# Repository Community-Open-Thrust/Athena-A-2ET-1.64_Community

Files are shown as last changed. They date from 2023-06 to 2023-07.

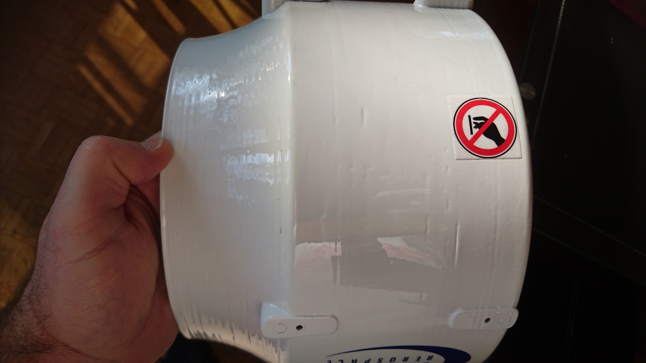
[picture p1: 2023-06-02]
Extra_Docs/Photos/Athena_DoNotTouch_Sticker_PrintedImprimé-preferably-round.JPG

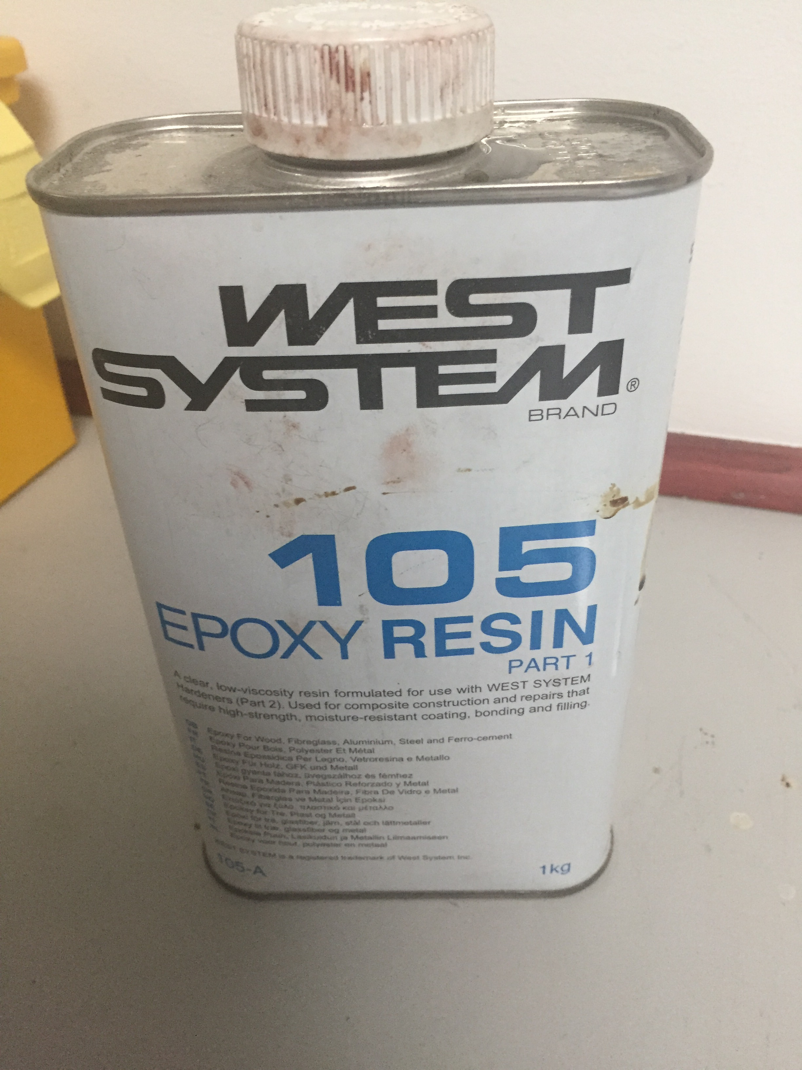
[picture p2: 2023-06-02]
Manufacturing_Info/Epoxy_Resin_105_West_System_IMG_6317.JPG

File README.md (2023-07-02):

# Athena-A-2ET Electric Ducted Fan (EDF) -  Community Edition
Athena-A 2ET - 2 stages electric ducted fan for static thrust - Community Edition - CERN-OHL-S (strongly reciprocal)

Athena_1-2ET-1 6x_Logo_BluePrint_Style

This is the repository for the Community Edition Release of the legacy to the community of makers from Neva Aerospace Ltd (UK) for the Athena Static Thrust Electric Ducted Fan (EDF) (Electric Turbine ) (Turbine électrique de poussée statique).
The Athena-A-2ET- is a 2 stages contra-rotative elecric ducted fan optimised for static thrust (hovering) in atmospheric conditions with maximum linear speed under 50kph (30mph).

The maximum thrust last checked in 2023 where between 3.7kgf to 4.1Kgf. It depends on the make of the Athena with 6S motors(2x550w) and e3D Printed parts.

# THE LICENSE IS CERN-OHL-S (Strongly Reciprocal) 
https://ohwr.org/cern_ohl_s_v2.pdf


Any further fork and/or modification must bear the following Notice as per chapter 1.10 of Definition of the OHL-s :
"acknowledgement of the Original Authors: Neva-Aero and the Human Team Members between 2013 and 2022 : F.M. Robert Vergnes, Laurent Martin, David Brotherton-Ratcliffe, Renaud-Pierre Blanpain, Daniel Schübeler, Sandro Pinent, Anthony Gambus, Tal Stokes, Valentin Bertrand, Tomas Valaitis, Louis Fourdan, Elie de Fonclare, Gilles Coïa, Domantas Brucas"

# About 3D Printing
All 3D printed parts must be in Polycarbonate in order to sustain mechanical constraints and temperature.

Only blades can be Printed in PLA with epoxy light coating.

All rotors must be balanced after assembly before mounting to the turbine.

# About using this repository
This Main repository will not change.

The Initial Commit Release date for the Main Repository is 30th of June 2023 and is for the Athena-A-2ET-1.64 (known as Athena 1.64 )

The main of repository will be locked to the initial commit to avoid losing information.

If you want to download or participate, please check the branch for the last version of the project.

If you want to participate please contact the Open-Thrust Core Team.

If you want to create a new branch for a new version please do fork or contact the Open-Thrust Core Team.

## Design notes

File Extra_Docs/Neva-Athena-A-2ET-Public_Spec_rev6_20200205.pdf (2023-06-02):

# Athena A

ELECTRIC VTOL TURB O-FAN

TURBIN E EL ECTRIQ UE D E POU SSÉE ST ATIQU E

ELEKTR O-TU RBO FA N

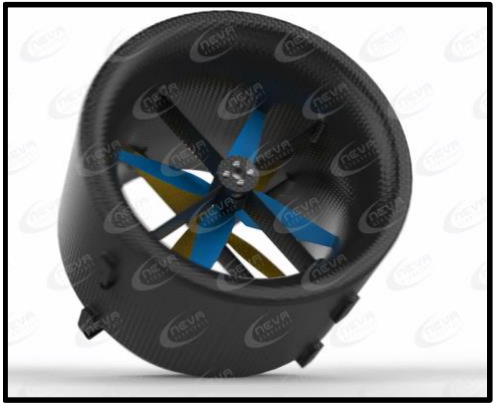
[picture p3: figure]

TECHNICAL SPECIFICATIONS – DATA SHEET | FEB. 2020

## The Neva Aerospace Athena Series are Electric Ducted Fans (EDF) engineered for efficient static flights, Vertical Take-Off

and Landing (VTOL).

## These devices are known by various names worldwide: Standschub optimimerter elektroimpeller or Elektro-turbofan in Germany, “Turbine électrique de poussée statique” in France and Electric VTOL Turbo-Fan (ETF) or static thrust Electric Ducted Fan (EDF) in the

UK and USA.

## Neva Athena Series turbines are the result of several years of R&D and provide high performance and remarkable efficiency. In particular they are designed for static thrust and are optimised for VTOL and STOL

operations.

# Key Key features:

### Safety is intrinsic in the design of all Neva EDFs, as all blades are caged: - Internal redundancy with 2 separate stages, 2 motors, and 2 ESCs (2ET-version) - Reduced size - High thrust density - Greater efficiency for static flights - high power loading as measured in

kg/kW.

### Athena A (autonomous) is offered in several variants: - 2ET: 2 stages counter-rotating (CW or CCW)*

(*) The residual torque of counter-rotating ETF can be selected as the rotation of the first stage. To be mentioned at purchase. By default we deliver 2 stages (2ET) as residual CW.

### Athena Series turbines are delivered fully assembled with Electronic Speed

Controllers (ESC), motors and propellers.

# Applications:

Typical usage for manned or unmanned aircraft: - Bespoke applications for medium sized UAS / UAV - Bespoke heavy-payload, high-safety UAV / UAA / AAM /UAM - Extreme sports (paraglider, base-jump, turbo-ski, etc…) - Security and Defence applications - Electric aviation: high -efficiency VTOL and slow speed linear flight - Airships: high efficiency thrust for VTOL & slow speed linear flight

### Athena-A-V1.x-2ET (2 stages counter-rotating)

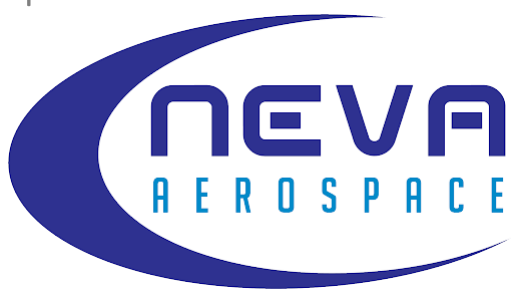
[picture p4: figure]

Copyright © 2015, 2016, 2017, 2018

Neva Aerospace Ltd.
Doc. Rev. 5.20

2/6

Made in Europe

# Contact: sales@neva-aero.com

Neva-Athena-A-2ET-Public_Spec_rev6_20200205.docx

Measurements on Athena-A-2ET-V1.6x Feb. 2018.

### Notes:

The residual torque of counter-rotating ETF can be selected as the rotation of the first stage. To be mentioned at purchase. By default we deliver 2 stages (2ET) as first stage CW with residual CW torque.
1.5x and 1.6x are in different composite materials and so have different density and weight ratio.
1.5x shroud: carbon composite, and other components: plastic composite.
1.6x all parts are plastic composite.
V1.5x and V1.6x include the ESC weight (ESC integrated within the turbine)

### Temperatures :

Operating temperatures: non-icing conditions only & avoid direct sunlight when not flying from -10 Degree Celsius to +50 Degree Celsius for Carbon shroud (1.5x)
from 0 Degree Celsius to +40 Degree Celsius for Plastic Composite shroud(1.6x)
Storage Temp: from 5 DegC to +35 DegC – no direct sunlight- dry storage50
Max Diameter of Turbine at Inlet | 250 mm
Rotor Assembly Diameter | 195 mm
Length of Shroud | 170 mmm
Weight of Turbine | 1.1 kg
Max Thrust | 4.0 kgf
Electrical Power at Max Thrust | 1.2 kW
Normal Operating Thrust | 2.9 Kgf
Power at Normal Operating Thrust | 0.8 kW
Supply Voltage | 22.4 V (6S)
Max Current | 55 A
| 0.92 Kgf @ 6.07 gf/We
Efficiency (Gross Power Loading) | 1.38 Kgf @ 5.18 gf/We
at various Thrust settings | 2.04 Kgf @ 4.32 gf/We
| 2.76 Kgf @ 3.85 gf/We
| 3.39 Kgf @ 3.33 gf/We
Material | Composite
Noise Level (@3m ) Outdoor | 84db at full power
Noise Level (@3m ) Indoor | 92dB at full power

### ATHENA-A-2ET-V1.64 (2 stages Contra-rotating)

3/6

# Contact: sales@neva-aero.com

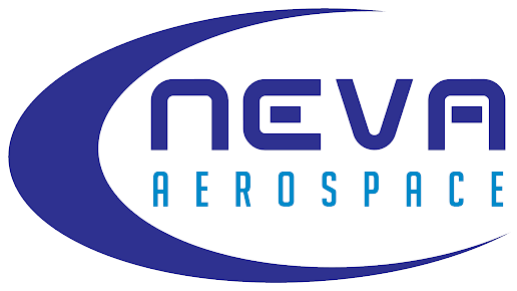
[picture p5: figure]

Neva-Athena-A-2ET-Public_Spec_rev6_20200205.docx

## ATHENA-A ELECTRIC VTOL TURBO-FAN Made in Europe

## Notes on Technical Specifications:

Units used:
International System of Units (SI Metric): kg= kilogram, g=gram, kgf=kilogram force means thrust measured in kilograms; g/We (or gf/W) means efficiency in gram-force-thrust per Watt electric consumed.
Weight & Control Systems:
ESC means Electronic Speed Controller
The weight of our turbofans includes shroud, motors, propellers, and motor holder(s) but not the ESCs.
ESCs are delivered together with the EDF.
Motors:
Depending on your applications we mount 2 types of electric motor with different power, please contact us for motor specifications.
Accuracies:
All figures are given with a +/- 5% accuracy.
All thrusts in gf or in kgf and efficiencies (power loadings) in gf/We or kgf/We represent gross values and are given with reference to the International Standard Atmosphere for dry air (ICAO 1964) and as such pertain to measurements at 15 degrees Celsius at 1013.25hPa and zero humidity.
Updates:
Specifications are subject to be updated without notice.
Please contact us to obtain the latest specifications.
Warranty Warning:
Any modification made to the ESC, motor, propellers, fan or shroud geometry, or over-clocking will void the warranty.
Icing condition: De-icing may not be fitted, and our electric turbofans are currently not acceptable for icing conditions.
Flight Level: Operational flight level up to 3281 ft (Feet) / 1000 M (Meter) Restrictions: Neva authorize and warrant the use of its electric ducted fans only for civilian applications up to 25kg MTOW aircraft (LT25) and lower than 3 000 ft. Shroud Warranty – outside of wearable parts:
Carbon shroud 3 years or 5 000 hrs
Plastic composite shroud 1 years or 2 000 hrs
Turbine Ingress Protection Code (IP): IP 53 . Please note that high level of dust or sand in atmosphere may wear blades or motor bearings more rapidly than usual.

IP
About Certifications & Flight Rules:
We make no warranties on the acceptability by the local regulator nor certification under local UAV/UAS regulation or Manned aircraft regulations. It is the full responsibility of the UAS/UAV integrator, aircraft manufacturer, to liaise with its certification body if/when need be.
Unmanned:
Our turbofans may be used for VLOS & BVLOS up to 25Kg MTOW depending on your region and local laws; and may not be suitable for BLOS according to your local rules. Applications with a MTOW higher than 25kg and/or above 3 000ft are at your own risks. To obtain warranty above MTOW 25Kg and/or 3 000 ft, you need to contact us.
Manned:
Our turbofans have to be certified within your aircraft under ULM or Prototype certification rules with your aircraft and may be suitable for VFR certification. If you embed our electric turbofan in a manned aircraft, you need to contact us to have an extension of warranty.
All information in this specification sheet is proprietary.
All images are non-contractual.

Patents (EU, USA, and INTL) granted and/or pending:
EU DM/089417, 2016-5567, US Application No. 35/5000,663 Copyright © 2015, 2016, 2017, 2018, 2019 – Neva Aerospace Ltd.

## Contact:

## Sales@Neva-Aero.com

Neva Aerospace Ltd.

### Sussex Innovation Centre Brighton BN1 9SB United Kingdom

# External Dimensions: Athena -A-2ET-V1.6x

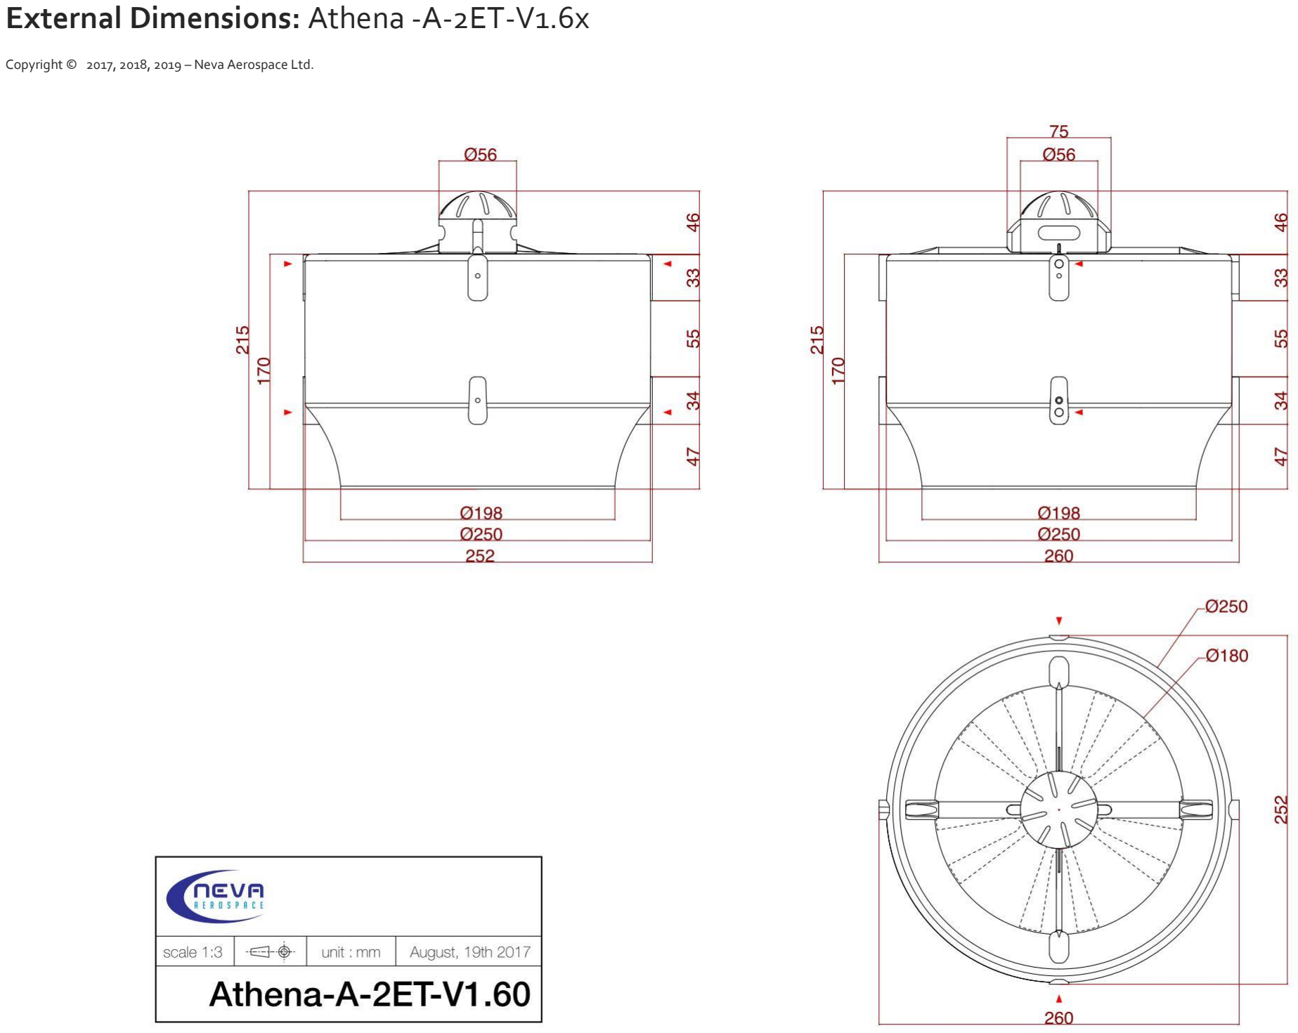
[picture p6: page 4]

Copyright © 2017, 2018, 2019 – Neva Aerospace Ltd.

## Technical Annex – Athena-A-2ET-V1.6x

## Efficiency Thrust vs Power – Athena-A-2ET-1.64 (6S)

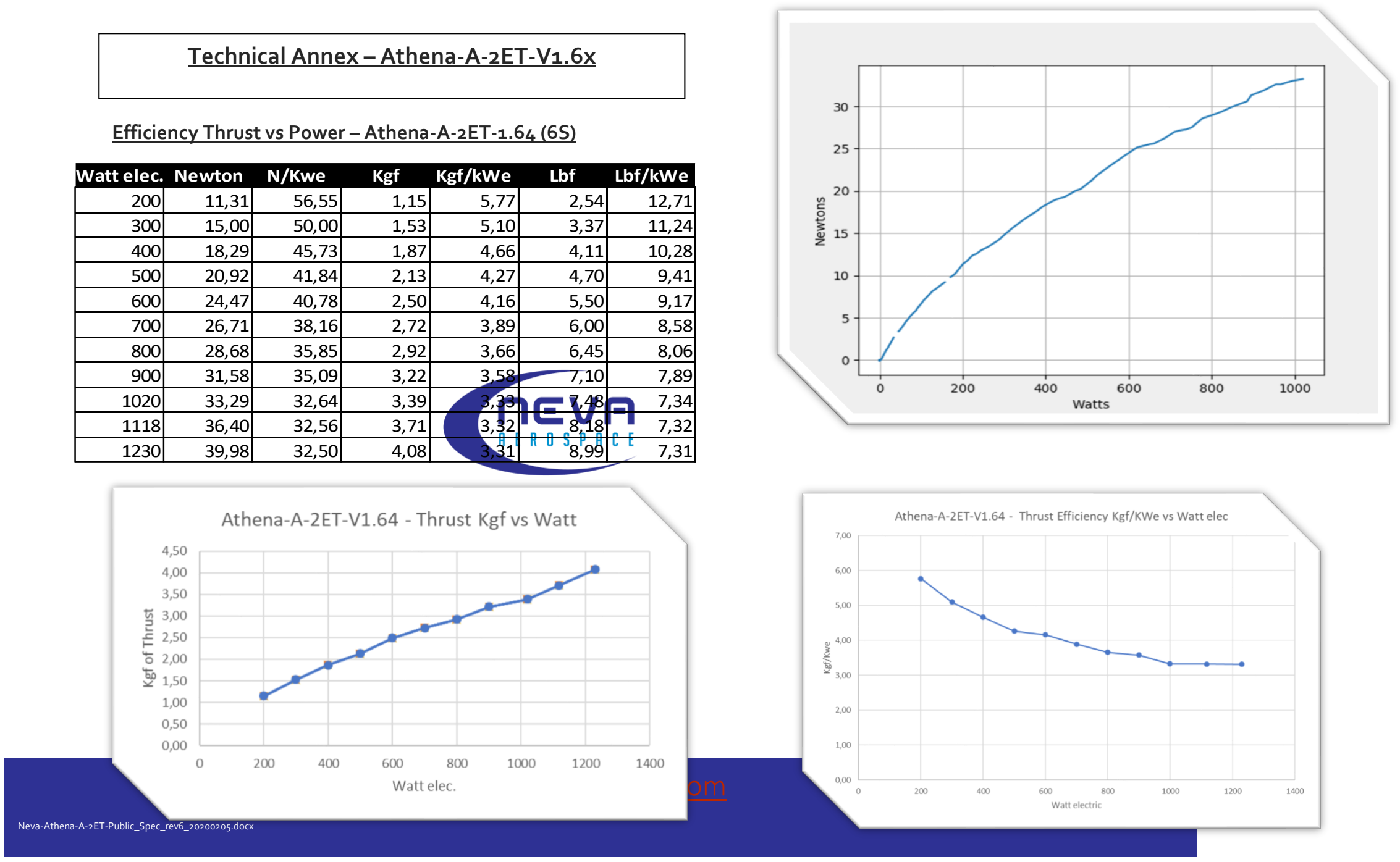
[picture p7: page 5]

5/6

# Contact: sales@neva-aero.com

Neva-Athena-A-2ET-Public_Spec_rev6_20200205.docx

Watt elec. Newton | N/Kwe | Kgf | Kgf/kWe | Lbf | Lbf/kWe
200 | 11,31 | 56,55 | 1,15 | 5,77 | 2,54 | 12,71
300 | 15,00 | 50,00 | 1,53 | 5,10 | 3,37 | 11,24
400 | 18,29 | 45,73 | 1,87 | 4,66 | 4,11 | 10,28
500 | 20,92 | 41,84 | 2,13 | 4,27 | 4,70 | 9,41
600 | 24,47 | 40,78 | 2,50 | 4,16 | 5,50 | 9,17
700 | 26,71 | 38,16 | 2,72 | 3,89 | 6,00 | 8,58
800 | 28,68 | 35,85 | 2,92 | 3,66 | 6,45 | 8,06
900 | 31,58 | 35,09 | 3,22 | 3,58 | 7,10 | 7,89
1020 | 33,29 | 32,64 | 3,39 | 3,33 | 7,48 | 7,34
1118 | 36,40 | 32,56 | 3,71 | 3,32 | 8,18 | 7,32
1230 | 39,98 | 32,50 | 4,08 | 3,31 | 8,99 | 7,31

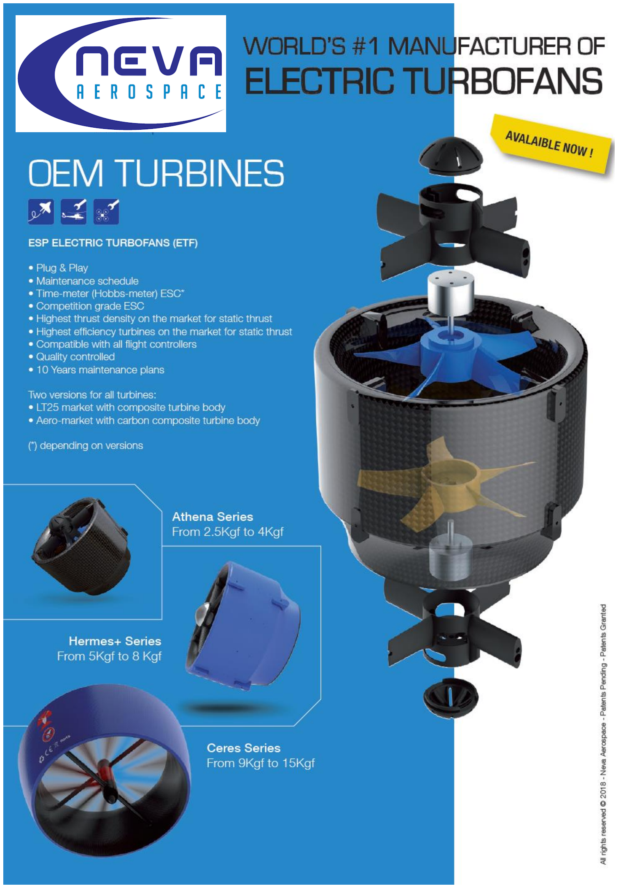
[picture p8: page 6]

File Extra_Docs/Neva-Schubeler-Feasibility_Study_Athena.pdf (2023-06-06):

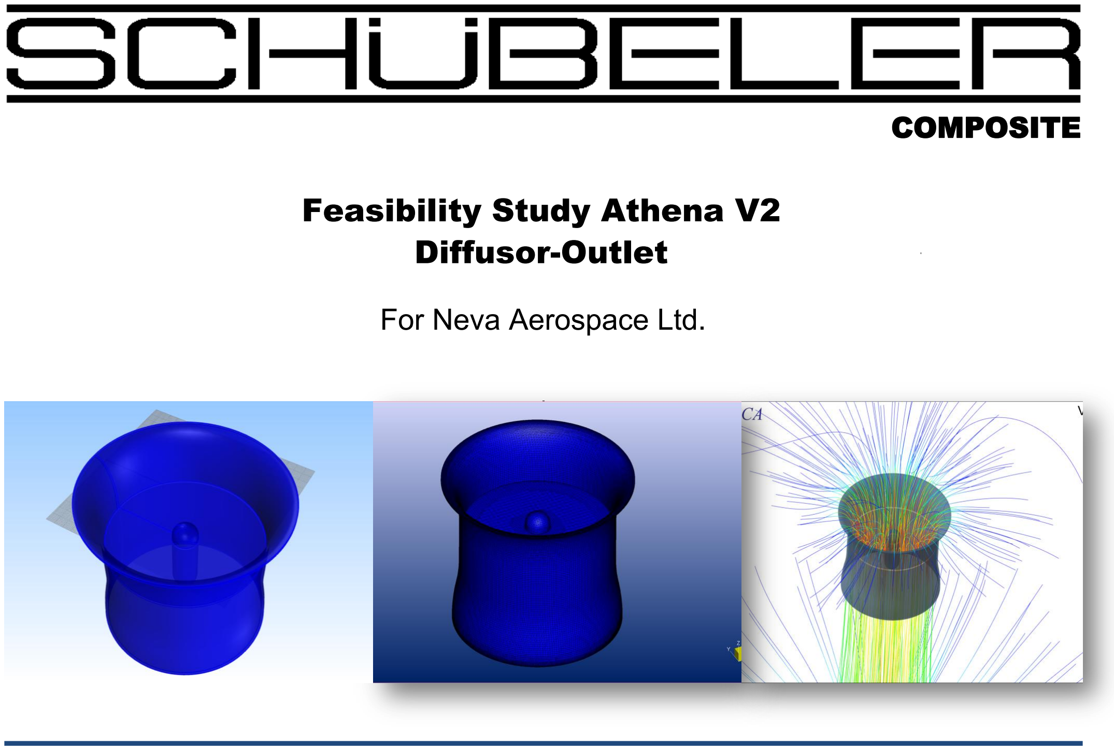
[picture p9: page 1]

COMPOSITE

Feasibility Study Athena V2

Diffusor⁻Outlet
For Neva Aerospace Ltd.

22.10.2015

Slide 2

Fa. Schübeler-Composite
Daniel Schübeler

Feasibility Study AthenaV2 Diffusor Outlet Dipl. Wirt.-Ing. Sandro Pinent

## Content

## 1. Specifications

## 2. Analytical Approach

## 3. CFD-Simulations

## 4. Conclusions

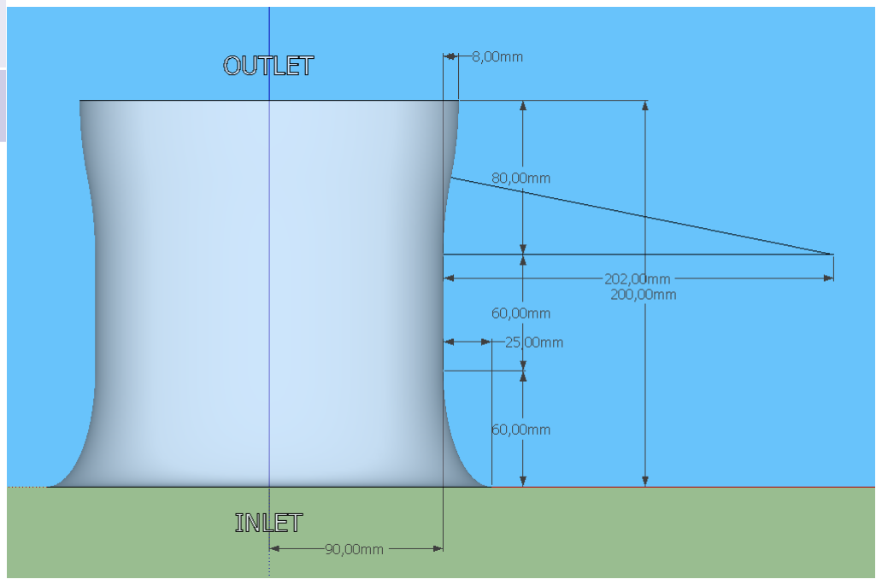
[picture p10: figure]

Slide 3

Fa. Schübeler-Composite
Daniel Schübeler

## 1. Specifications

| Athena V2
Density [kg/m³] | 1,25
Shroud Diameter [mm] | 180
Hub Diameter [mm] | 30
v0 [m/s] | 0
Thrust [N] | ~40 N

Slide 4

Fa. Schübeler-Composite
Daniel Schübeler

## 2. Analytical Approach

Where is the Lift generated?

- Momentum change

OR

- Thrust due to pressure distribution and viscous stress on solids

### v mv

dt

### dm T I

### I mv

- =
= =

=

ò | ò
= | · · | +
solid | Asolid
viscous | solid
A
T | p n dAsolid | τ | dA

## 2. Analytical Approach

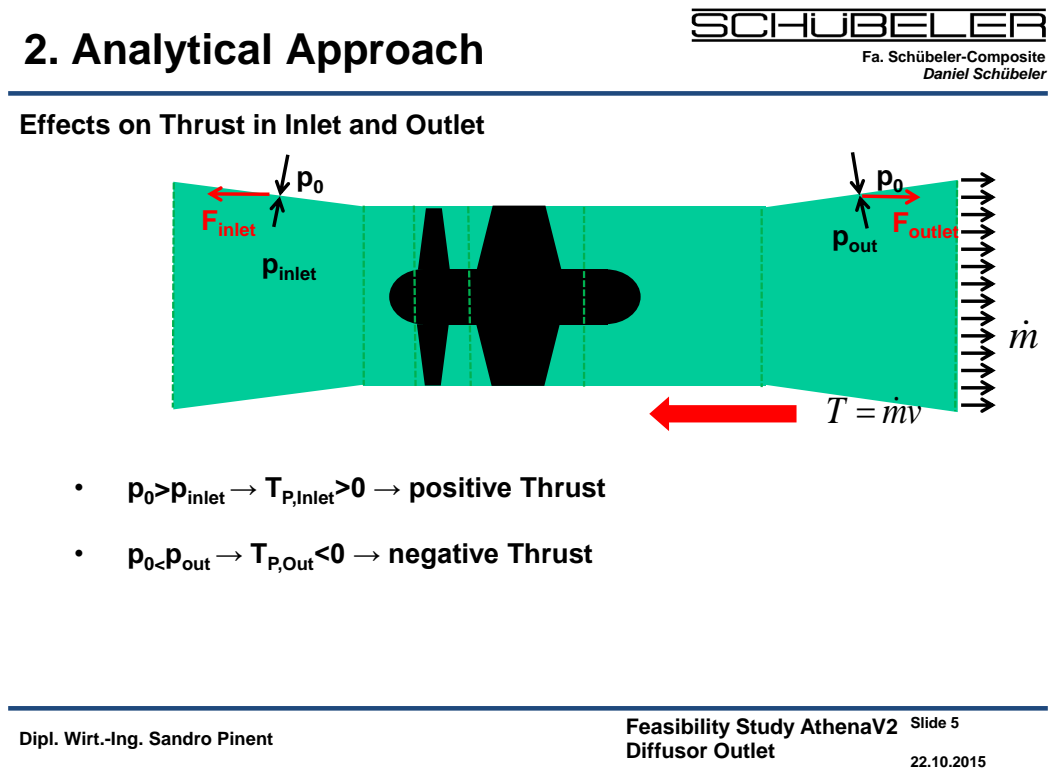
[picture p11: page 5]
Slide 5; Daniel Schübeler; pinlet; Finlet; pout; Foutlet

Fa. Schübeler-Composite

Effects on Thrust in Inlet and Outlet

• p0>pinlet→ TP,Inlet>0 → positive Thrust

• p0<pout → TP,Out<0 → negative Thrust

## 2. Analytical Approach

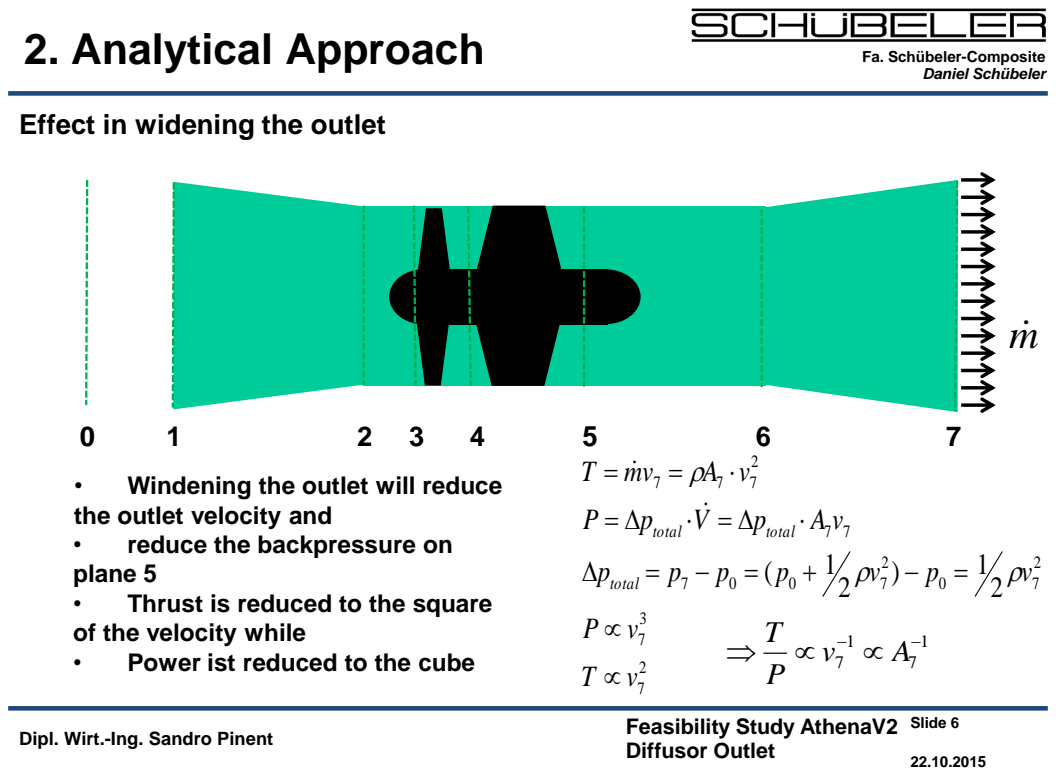
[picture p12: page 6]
Slide 6; Daniel Schübeler; total

Fa. Schübeler-Composite

Effect in widening the outlet

• Windening the outlet will reduce
the outlet velocity and
• reduce the backpressure on
plane 5
• Thrust is reduced to the square
of the velocity while
• Power ist reduced to the cube

## 2. Analytical Approach

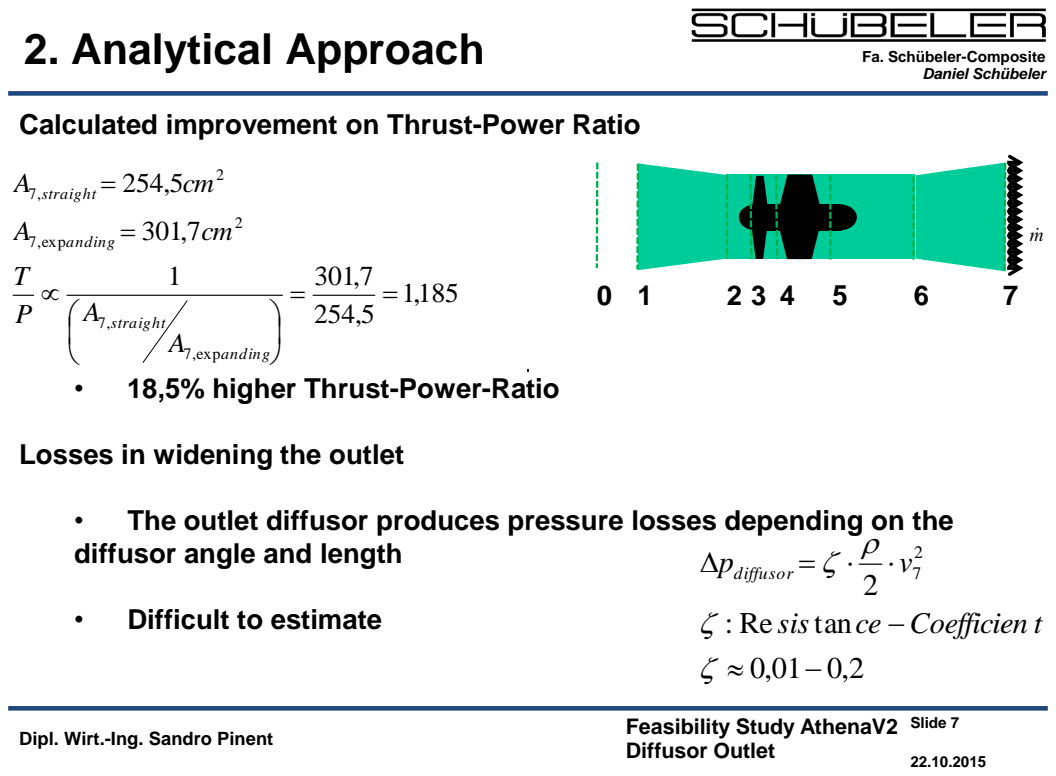
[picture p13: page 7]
Slide 7; Daniel Schübeler; tan; sis; ce Coefficien t; v diffusor; 7,exp; anding; straight

Fa. Schübeler-Composite

Calculated improvement on Thrust-Power Ratio

• 18,5% higher Thrust-Power-Ratio

Losses in widening the outlet

• The outlet diffusor produces pressure losses depending on the
diffusor angle and length

• Difficult to estimate

Slide 8

Fa. Schübeler-Composite
Daniel Schübeler

## 2. Analytical Approach

Unlimited Thrust?

- In Theory, yes
- Until the diffusor losses are bigger than the Thrust increase
- Reducing the outlet velocity means loss of agility
- What are the limits for the diffusor?

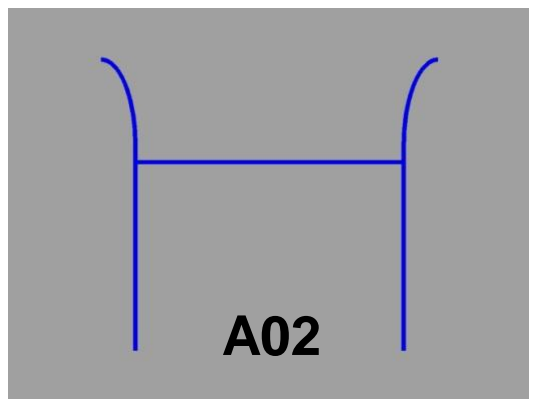
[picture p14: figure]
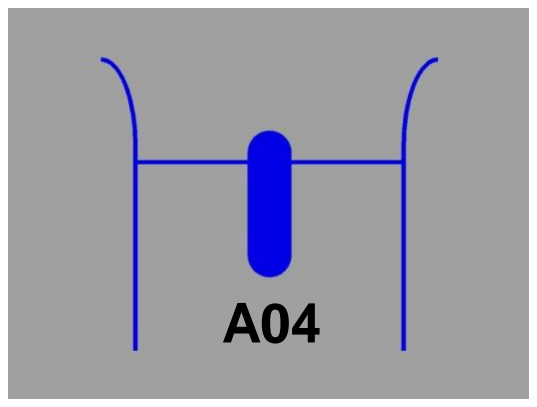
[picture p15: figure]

Slide 9

Fa. Schübeler-Composite
Daniel Schübeler

## 3. CFD-Simulations

Geometry:
- 4 Geometries calculated
- With hub and without hub
- With expanding nozzle and without

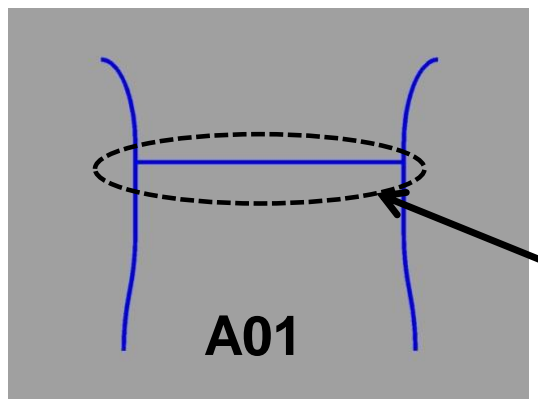
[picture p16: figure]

A03 | A04

Actuator Disc:
-Outlet at upper side
-Inlet at lower side
-same massflow

## 3. CFD-Simulations

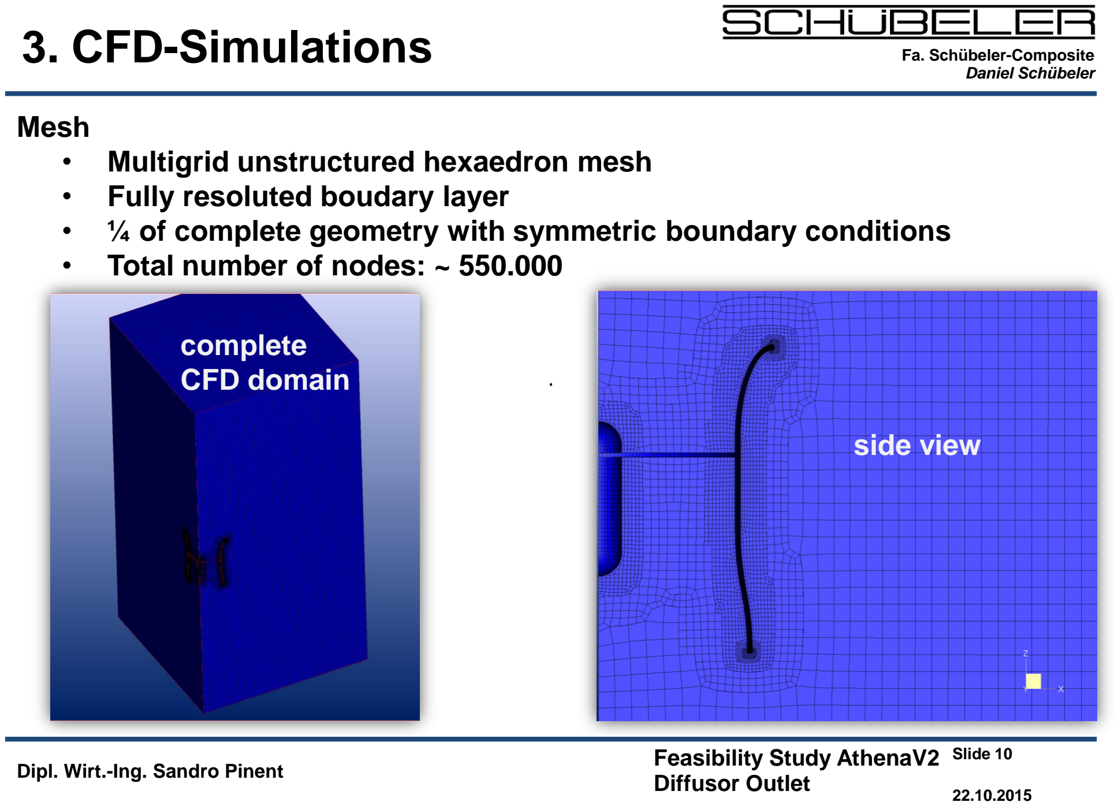
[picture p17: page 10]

Slide 10

Fa. Schübeler-Composite
Daniel Schübeler

Mesh
- Multigrid unstructured hexaedron mesh
- Fully resoluted boudary layer
- ¼ of complete geometry with symmetric boundary conditions
- Total number of nodes: ~ 550.000

complete
CFD domain

side view

## 3. CFD-Simulations

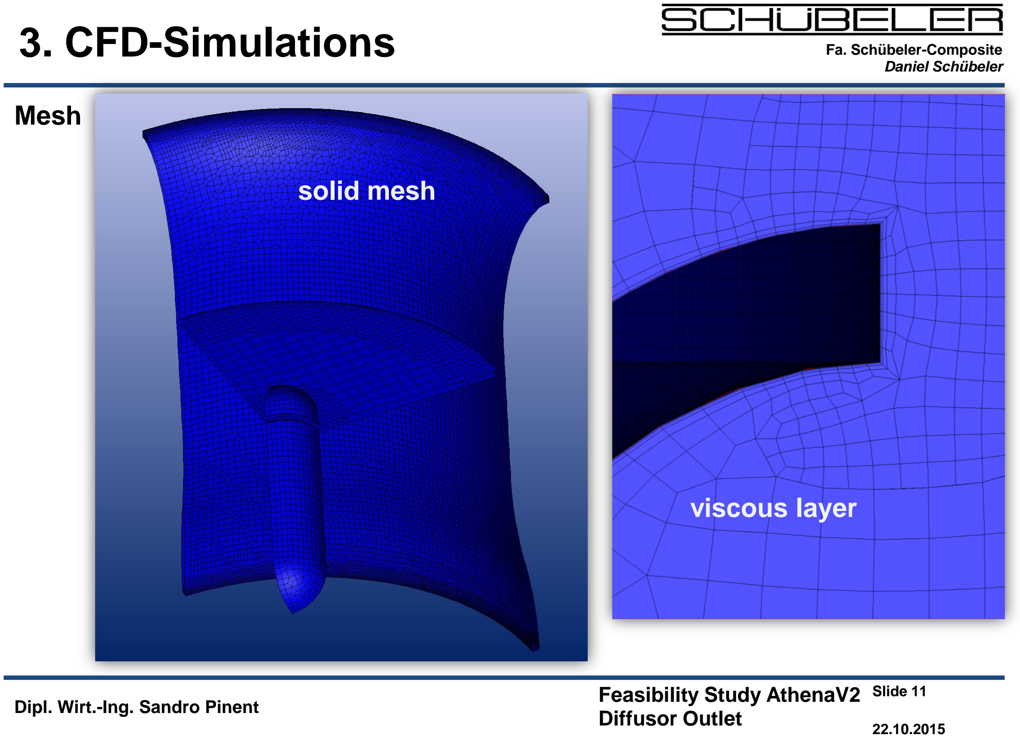
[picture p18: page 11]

Slide 11

Fa. Schübeler-Composite
Daniel Schübeler

Mesh

solid mesh

viscous layer

Slide 12

Fa. Schübeler-Composite
Daniel Schübeler

## 3. CFD-Simulations

Solver Setting

- Compressible fluid model „Air Perfect“
- Mathemetical model: Navier Stokes
- Spalart Almaras turbulence model
- CFL number: 3
- Steady state

Slide 13

Fa. Schübeler-Composite
Daniel Schübeler

## 3. CFD-Simulations

Boundary Conditions

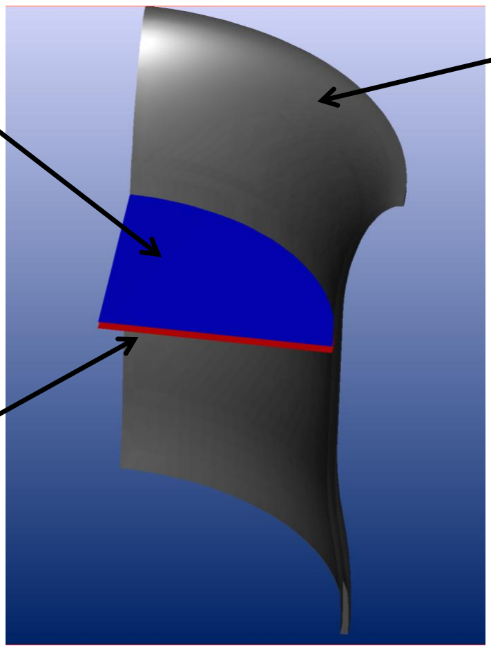
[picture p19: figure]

Outlet:
1,049 kg/s

Inlet:
1,049 kg/s

Solids:
smooth Wall

Externals:
v=0 m/s
p=102325
T=288,15 K

## 3. CFD-Simulations

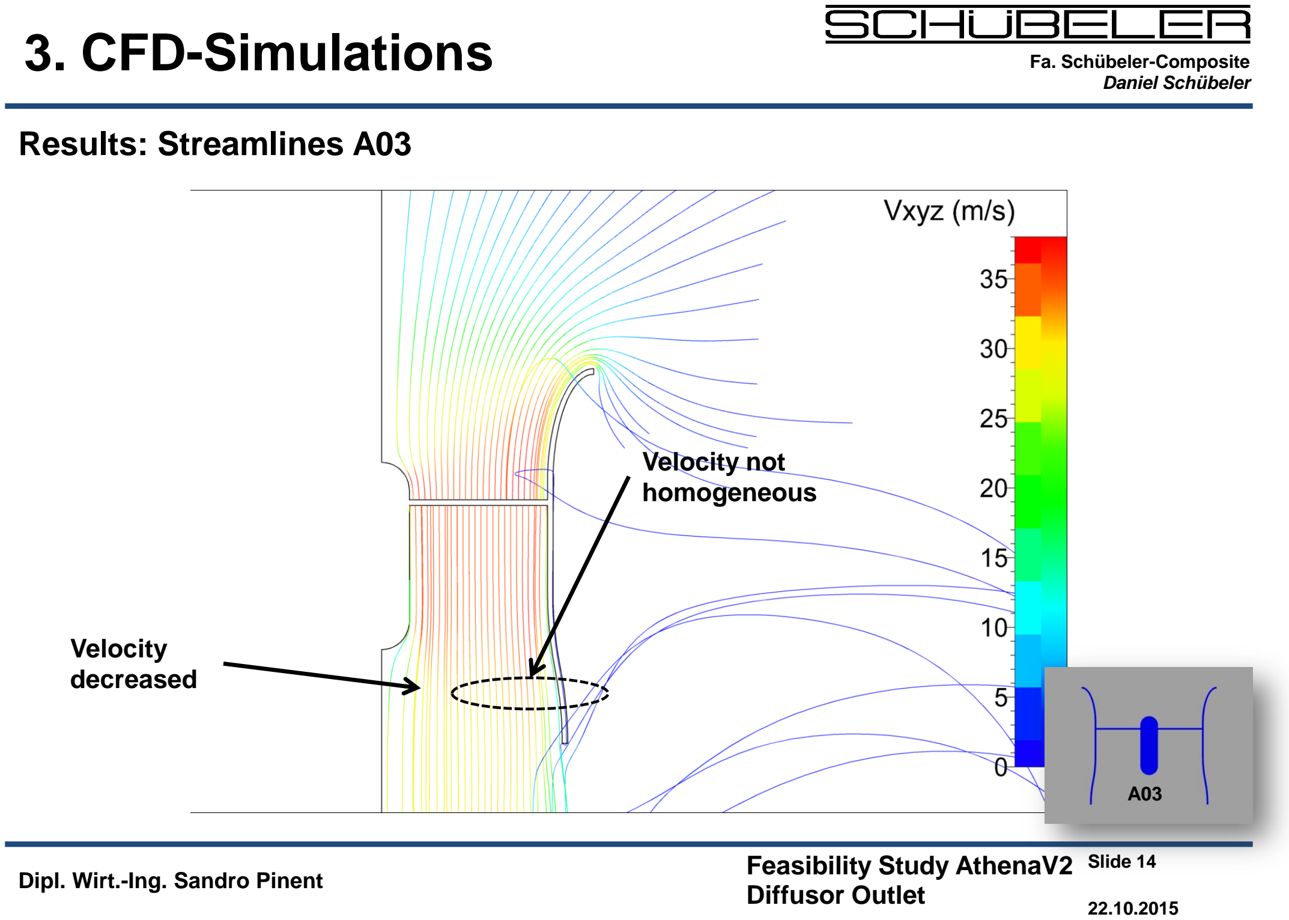
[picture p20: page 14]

Slide 14

Fa. Schübeler-Composite
Daniel Schübeler

Results: Streamlines A03

Velocity
decreased

Velocity not
homogeneous

A03

## 3. CFD-Simulations

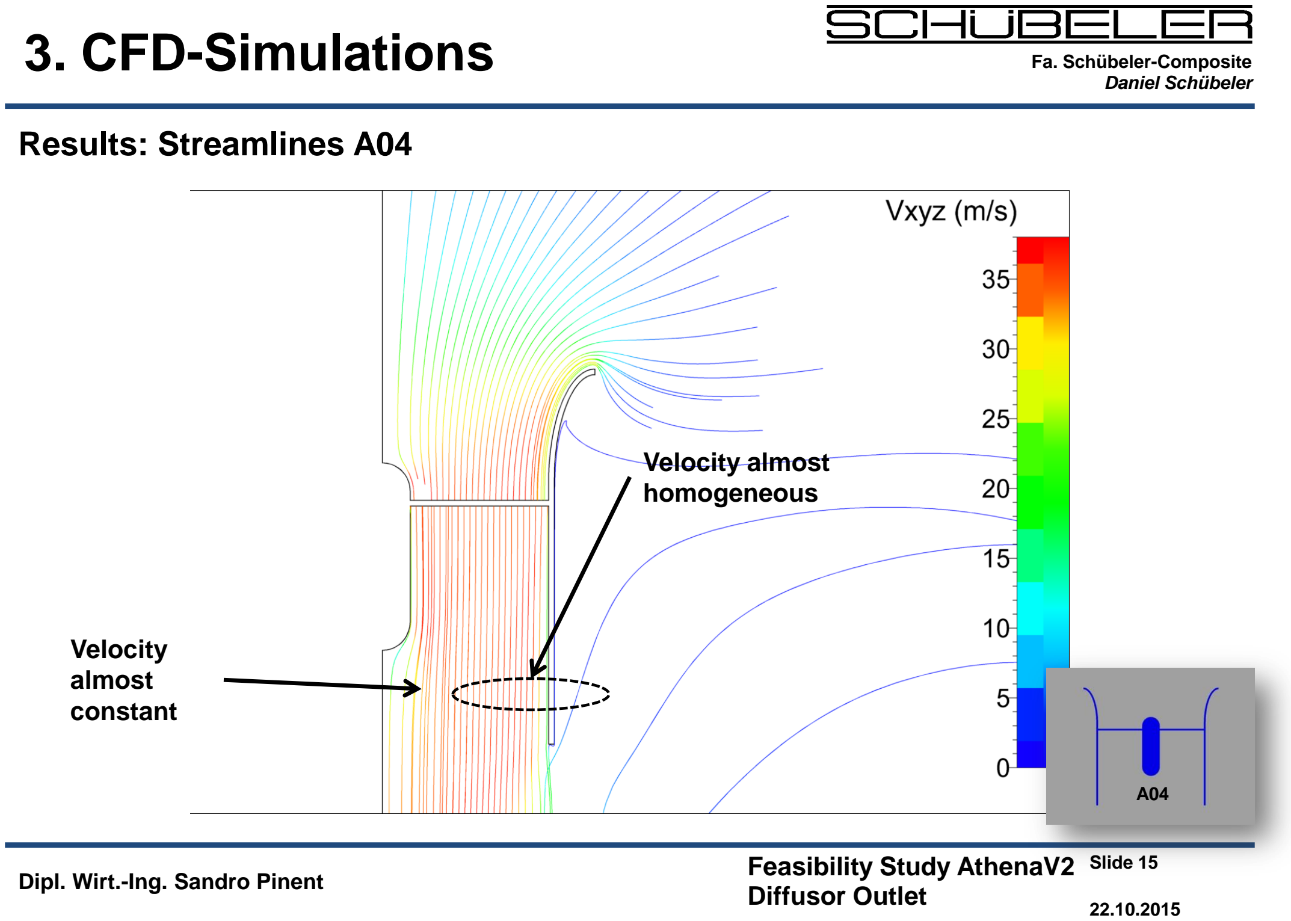
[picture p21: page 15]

Slide 15

Fa. Schübeler-Composite
Daniel Schübeler

Results: Streamlines A04

Velocity
almost
constant

Velocity almost
homogeneous

A04

## 3. CFD-Simulations

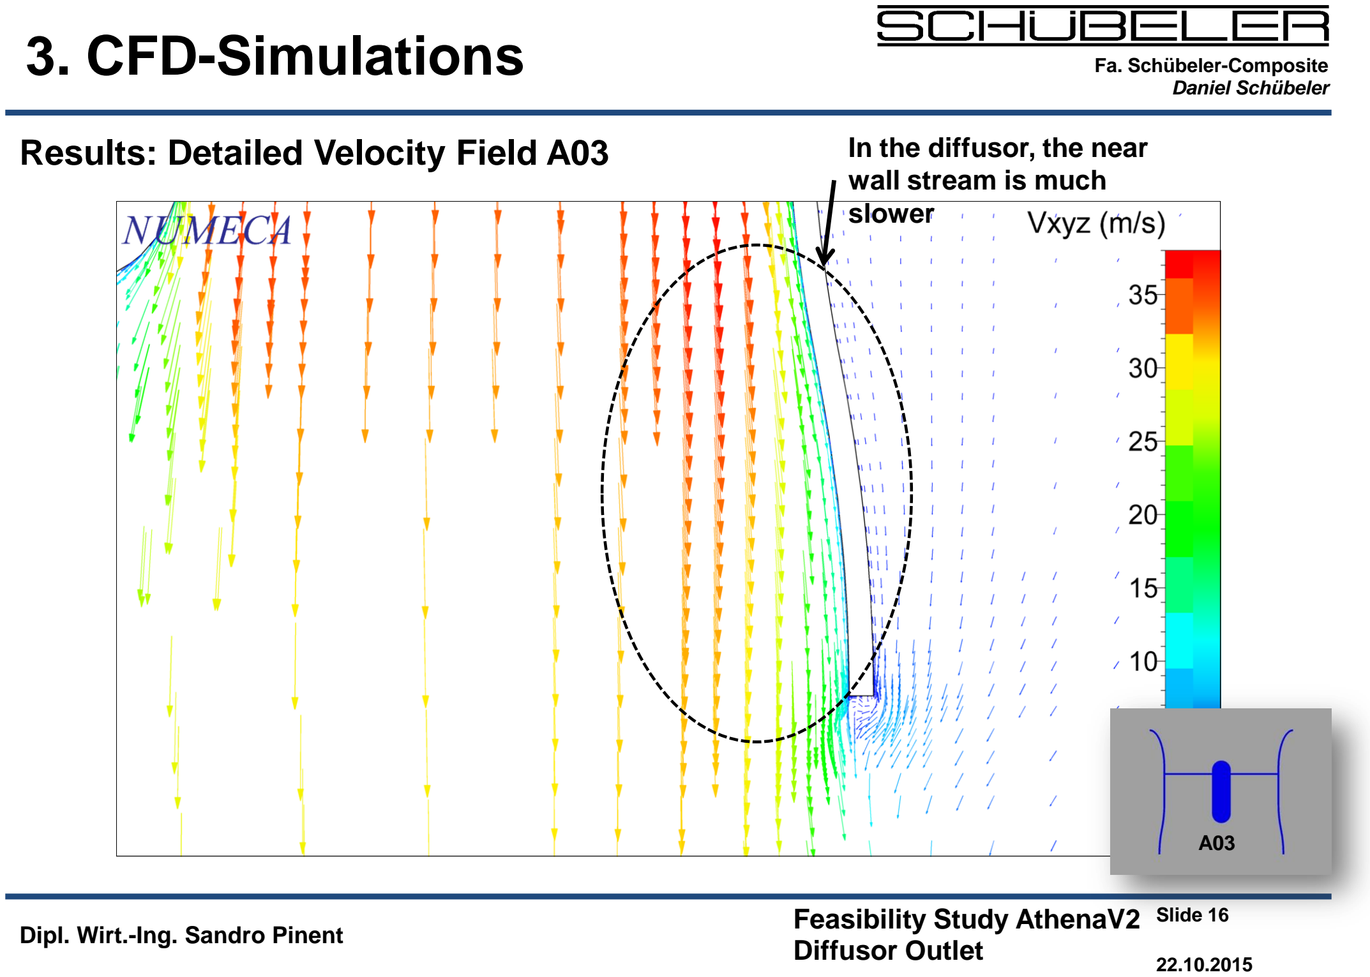
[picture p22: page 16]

Slide 16

Fa. Schübeler-Composite
Daniel Schübeler
Results: Detailed Velocity Field A03 | In the diffusor, the near wall stream is much slower

A03

## 3. CFD-Simulations

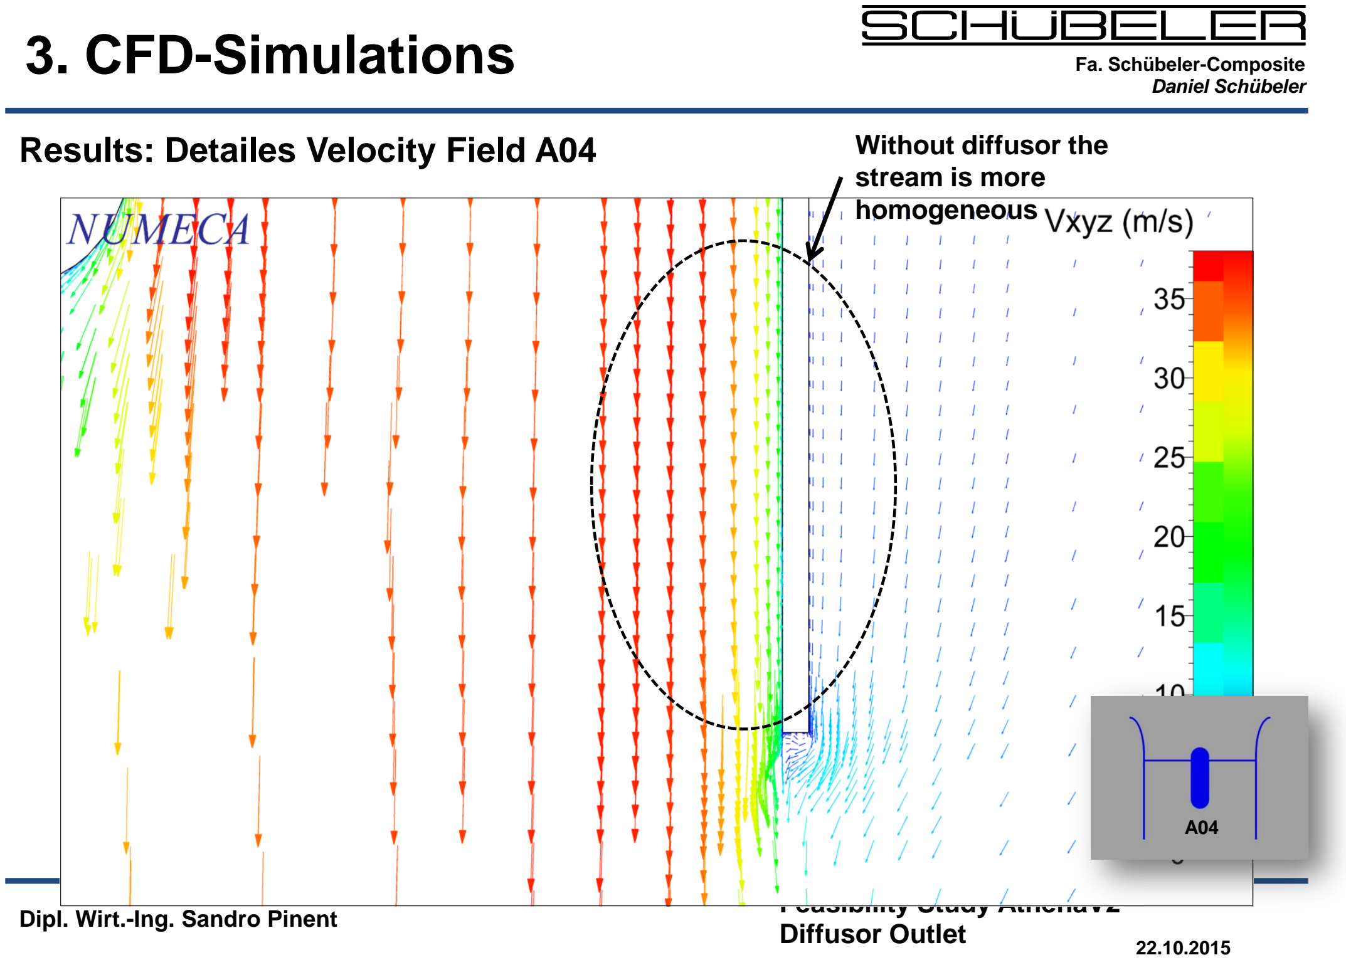
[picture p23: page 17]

Slide 17

Fa. Schübeler-Composite
Daniel Schübeler
Results: Detailes Velocity Field A04 | Without diffusor the stream is more homogeneous

A04

## 3. CFD-Simulations

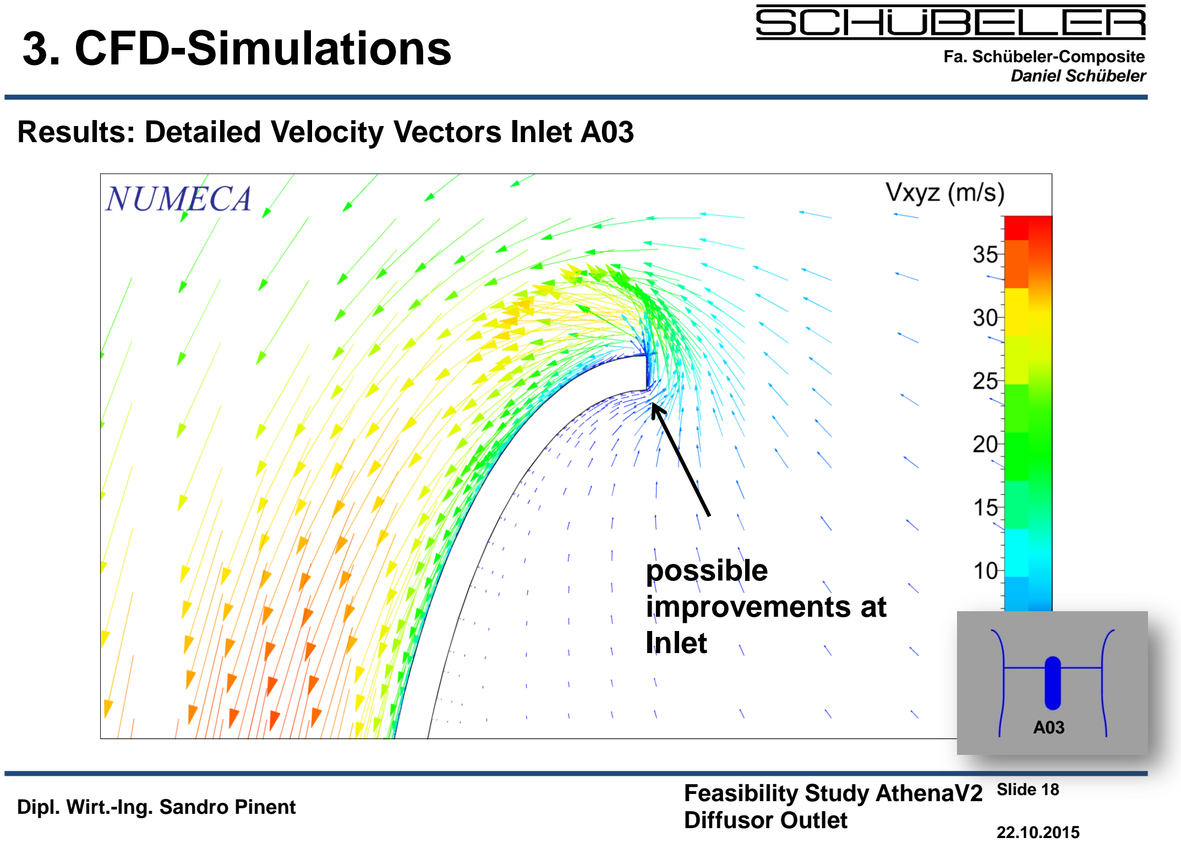
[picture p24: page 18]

Slide 18

Fa. Schübeler-Composite
Daniel Schübeler

Results: Detailed Velocity Vectors Inlet A03

A03

possible
improvements at
Inlet

## 3. CFD-Simulations

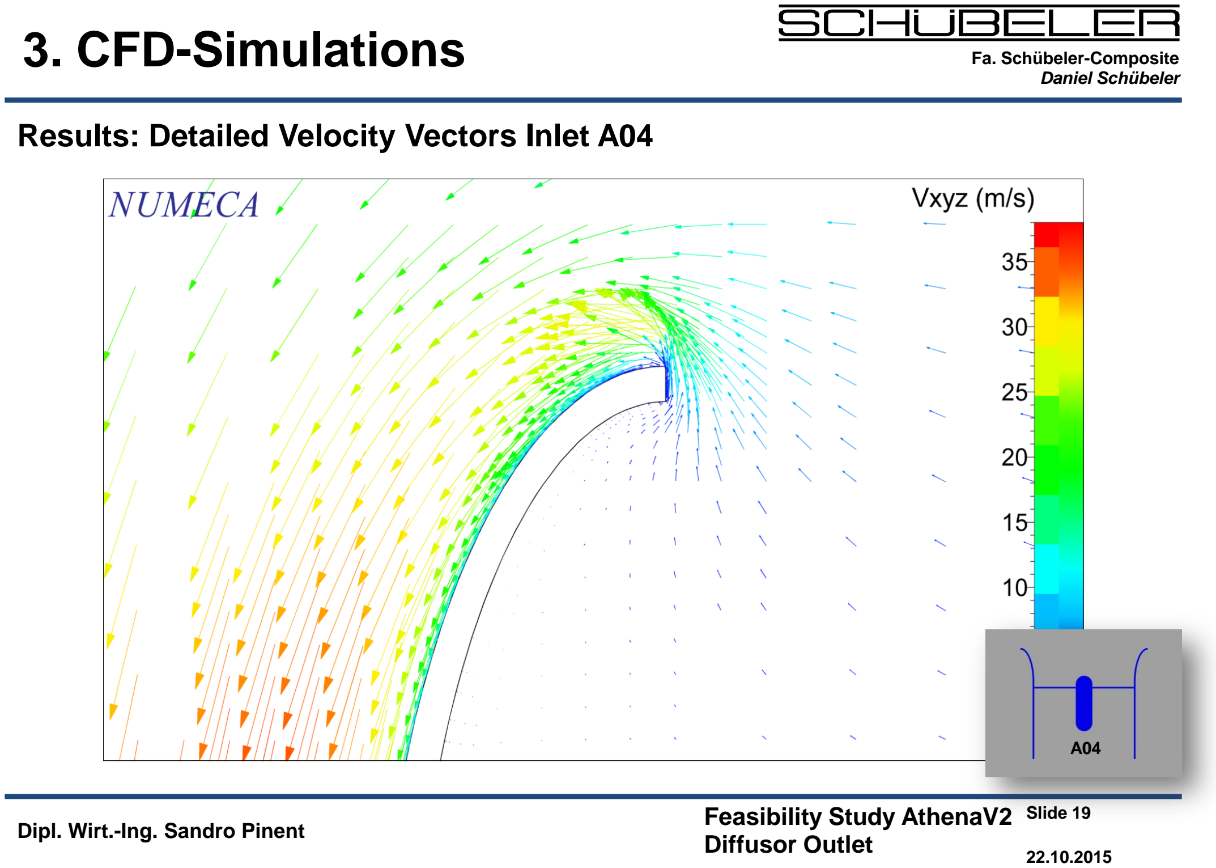
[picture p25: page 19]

Slide 19

Fa. Schübeler-Composite
Daniel Schübeler

Results: Detailed Velocity Vectors Inlet A04

A04

## 3. CFD-Simulations

Slide 20

Fa. Schübeler-Composite
Daniel Schübeler

Results: Total and Static Pressure A03

A03

## 3. CFD-Simulations

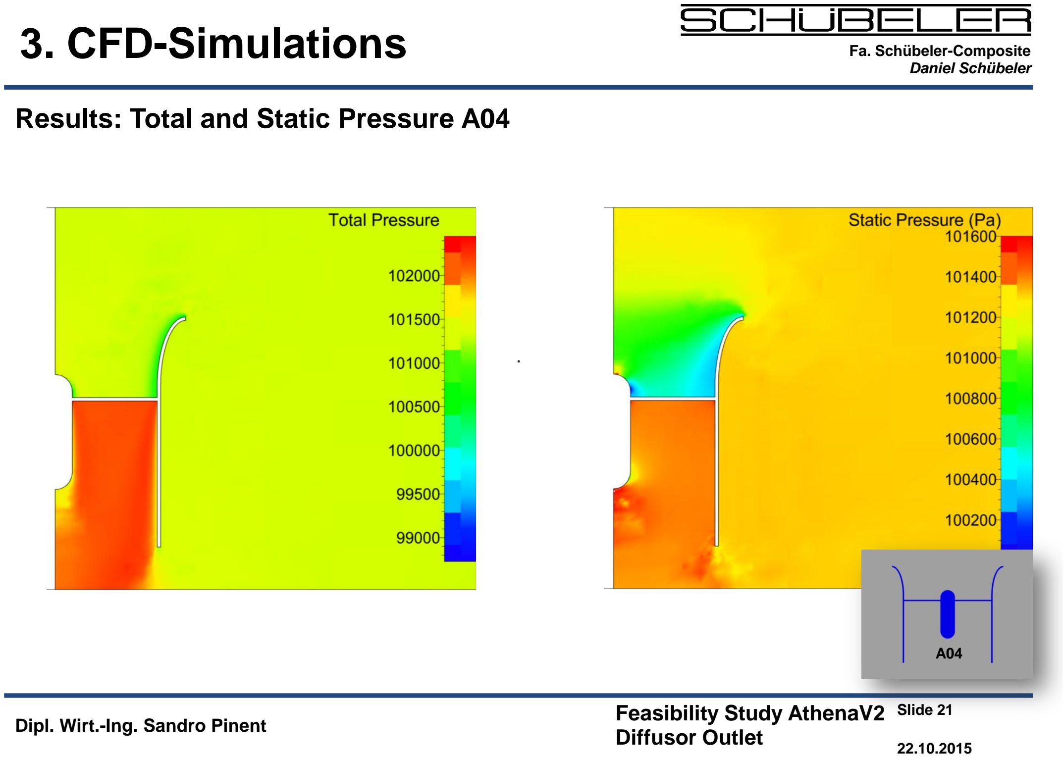
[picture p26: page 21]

Slide 21

Fa. Schübeler-Composite
Daniel Schübeler

Results: Total and Static Pressure A04

A04

Fa. Schübeler-Composite
Daniel Schübeler

## 3. CFD-Simulations

Results: Visualization of the Pressure Forces in Z-Direction A03

Slide 22

Fa. Schübeler-Composite
Daniel Schübeler

## 3. CFD-Simulations

Results: Visualization of the Pressure Forces in Z-Direction A04

Slide 23

Slide 24

Fa. Schübeler-Composite
Daniel Schübeler

## 3. CFD-Simulations

Results: Comparsion

- The diffusor outlet has 23% better Thrust-Power-ratio
- Analytically only 18% ... ?
- Only the hydraulical Power is considerated, no fan, nor motor efficiency
- To achieve this improvement, the aerodynamic rotor has to be optimized for each case. (Optimum rotor for A03 is other than A04)
- The improvement works only for static thrust
| T[N] Momentum change (mf*v) | vf[m³/s] | ptot,3 [Pa] | ptot,5 [Pa] | Δp [Pa] | Phydr [W] | T/Phydr [N/kW]
A03 | 30,45 | 0,856 | 101220 | 101867 | 647 | 553,8 | 54,9
A04 | 35,88 | 0,855 | 101220 | 102160 | 940 | 803,9 | 44,6

Fa. Schübeler-Composite
Daniel Schübeler

## 4. Conclusions

Outlook

- It may be interesting to push the diffusor to the limits
- Find the optimum diffusor in trems of diameter, length and shape
- Investigate how the diffusor behaves at other power setting

Slide 25

- Perform a complete CFD-Calculation including the complete rotating fan

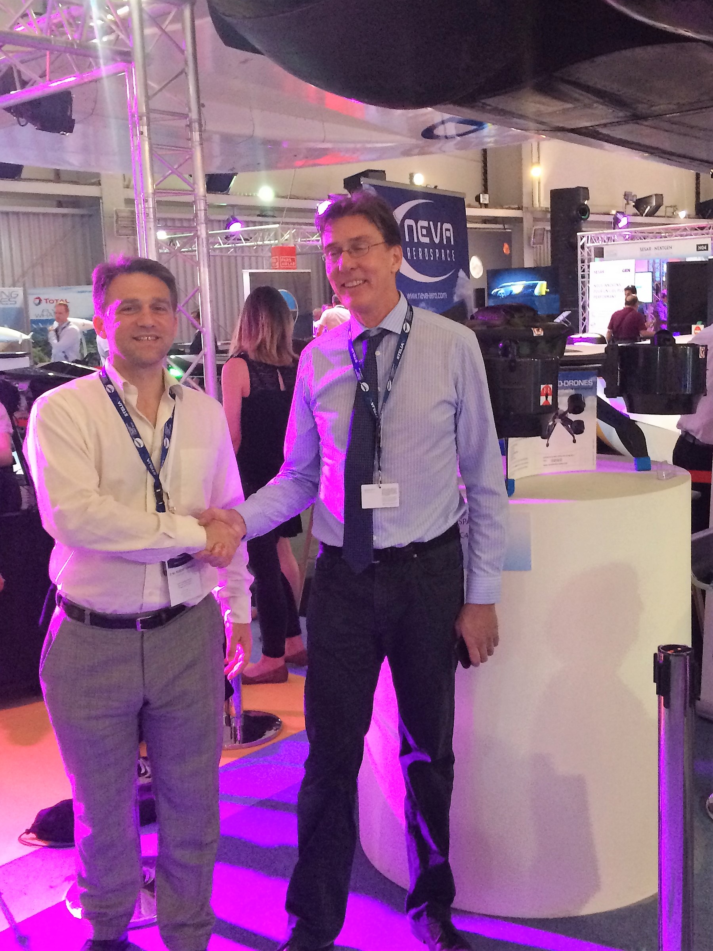
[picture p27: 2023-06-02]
Extra_Docs/Photos/Exhibitons_various/R_Vergnes_D_Ratcliffe_IMG_0991.JPG

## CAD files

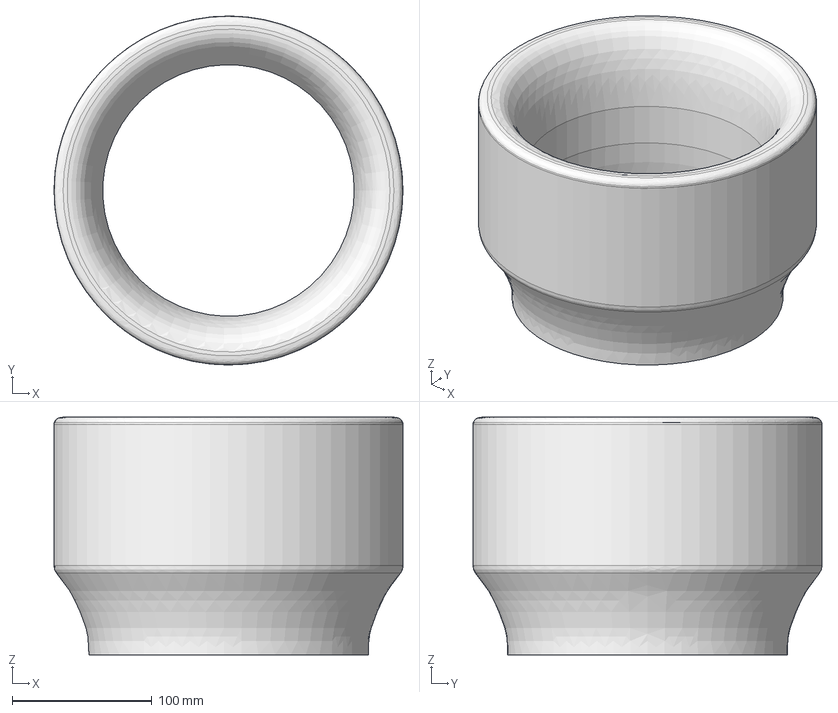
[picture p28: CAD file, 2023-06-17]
CAD_3D/STEP/ATHENA-SHO-NAKED-V1.64.step
249.7 x 249.7 x 170.1 mm

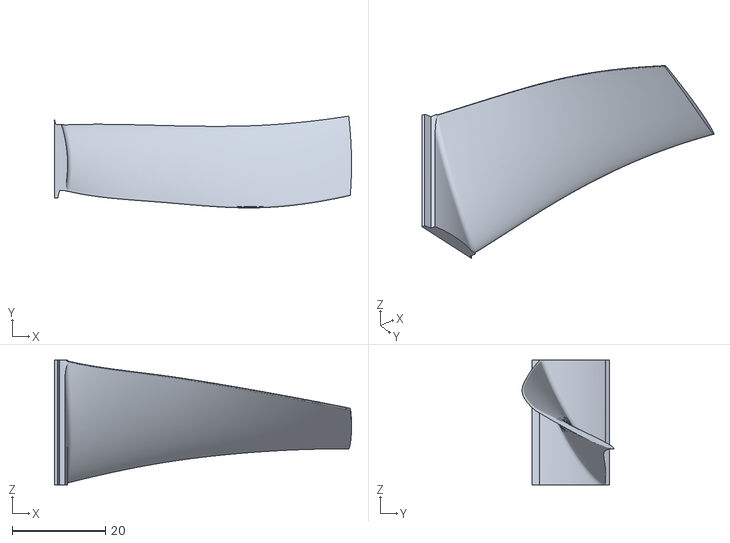
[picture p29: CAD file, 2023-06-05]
CAD_3D/STL/BLA-OUTLET-2A-A-164.stl
63.8 x 19.7 x 26.7

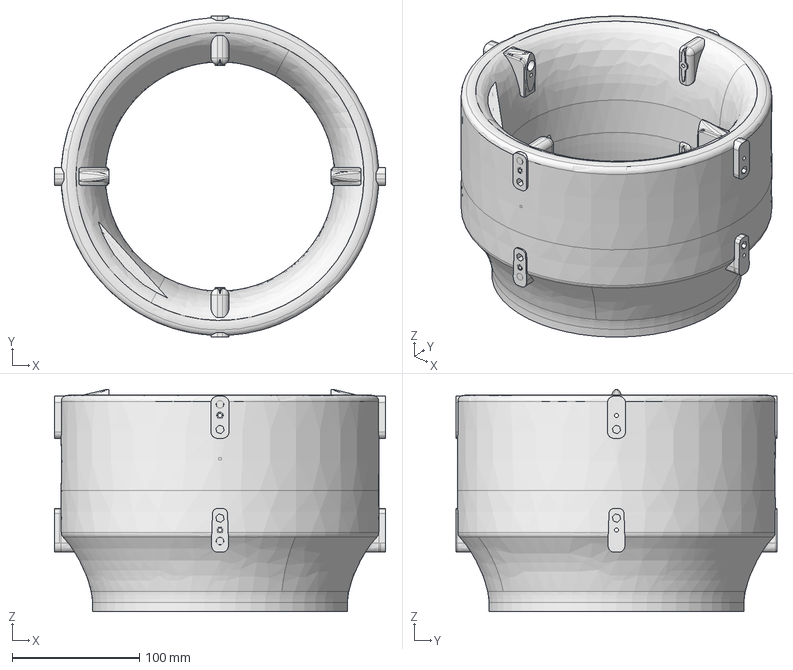
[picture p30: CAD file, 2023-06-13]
CAD_3D/STEP/Athena v1.63 Shroud v37 v1.step
260.0 x 252.0 x 174.6 mm

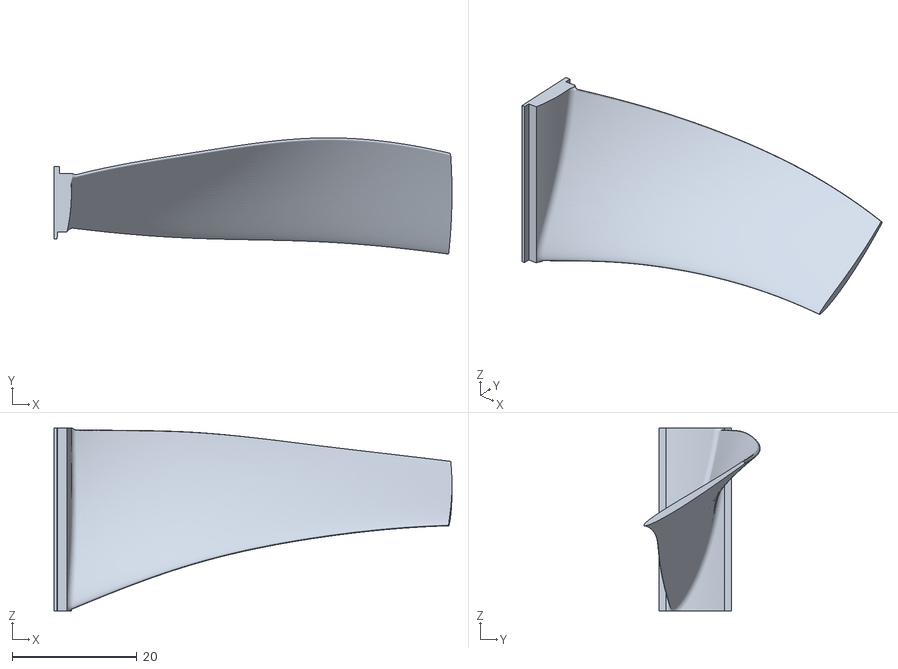
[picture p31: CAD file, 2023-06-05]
CAD_3D/STL/BLA-INLET-1A-1-164.stl
63.8 x 18.6 x 29.3

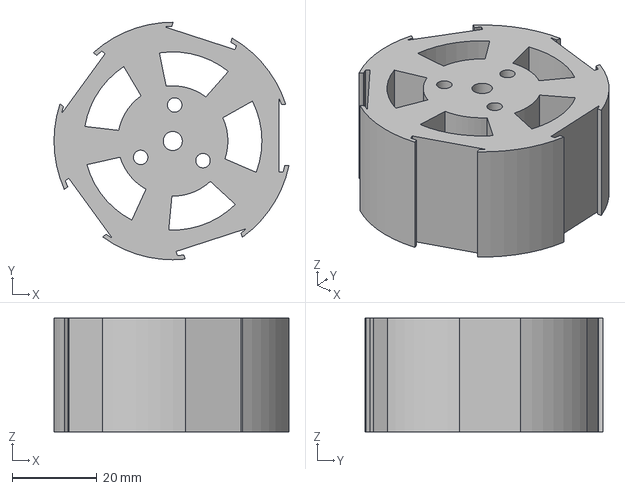
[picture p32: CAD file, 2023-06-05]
CAD_3D/STEP/ROT-OUTLET-2A-A-1.64.step
55.4 x 56.0 x 26.8 mm

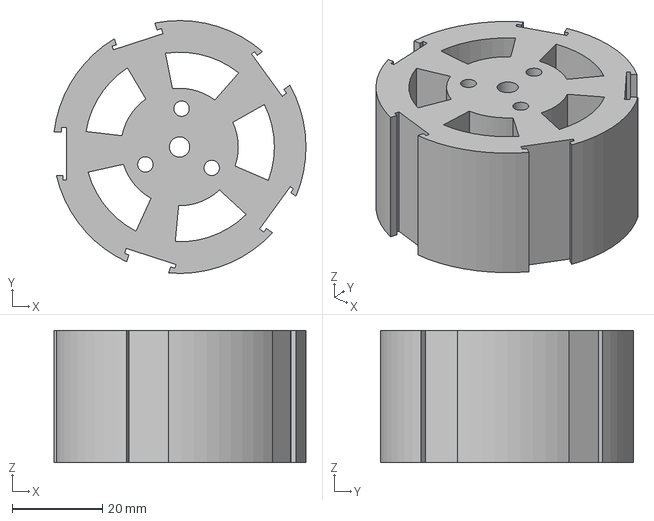
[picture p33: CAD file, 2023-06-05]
CAD_3D/STEP/ROT-INLET-1A-A-1.64.step
55.8 x 56.0 x 29.3 mm

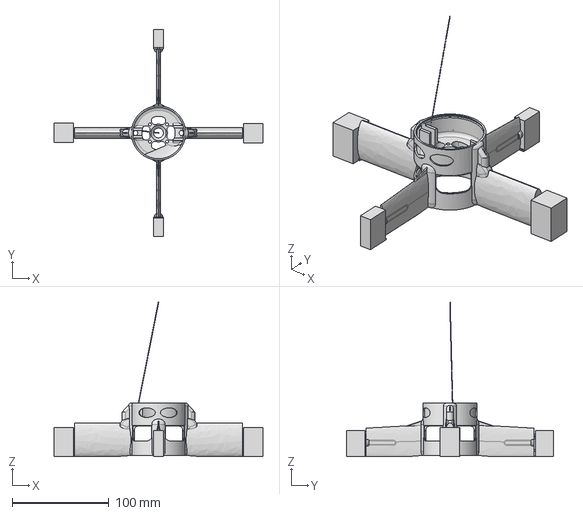
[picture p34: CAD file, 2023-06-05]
CAD_3D/STEP/STATOR-A-164_Arm.stp
215.8 x 213.8 x 159.5 mm

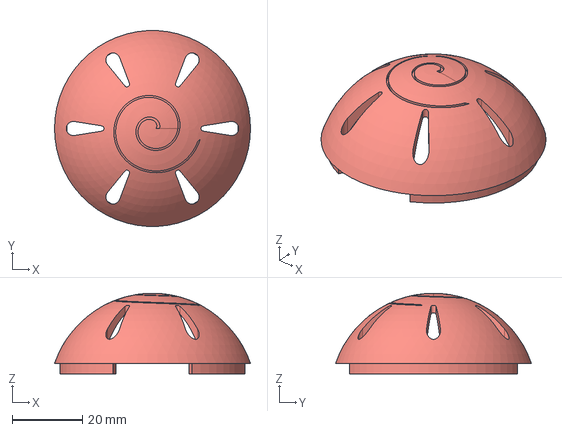
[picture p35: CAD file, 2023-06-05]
CAD_3D/STEP/COOLING-CAP-A-164.stp
56.0 x 55.9 x 23.0 mm

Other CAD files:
CAD_3D/STEP/Inlet-BLA-164.step
CAD_3D/STEP/Outlet-BLA-164.step
CAD_3D/STL/ATHENA-SHO-NAKED-V1.64.stl
CAD_3D/STL/COOLING-CAP-A-164.stl
CAD_3D/STL/ROT-INLET-1A-A-1.64.stl
CAD_3D/STL/ROT-OUTLET-2A-A-1.64.stl
CAD_3D/STL/STATOR-A-164_Arm.stl

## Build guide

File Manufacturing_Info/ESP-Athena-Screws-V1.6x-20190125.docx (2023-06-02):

# ATHENA-A-@ET-V1.6x - La Visseries The Screws

Date: 25/01/2019 - issued by : TVL / reviewed by: RFV

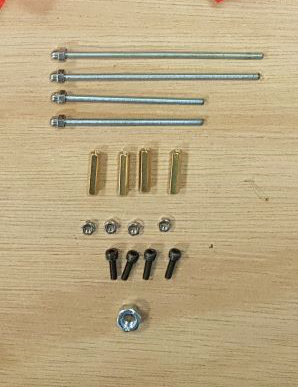
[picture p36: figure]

For each turbine:

# 1. Screws / Vis:

4x M3 10mm,

2 x M3 60mm

2 x M3 screws 80mm.

Nuts / Ecrous:

4 x M3 (standard - no nylstop)

1 x M6 (standard - no nylstop)

# 2. Female Thread Hexagonal / Insert Rallonge Hexagonale:

M3 10mm (better)

/ - CONFIDENTIAL INFORMATION - NEVA AERO / ESP SAS

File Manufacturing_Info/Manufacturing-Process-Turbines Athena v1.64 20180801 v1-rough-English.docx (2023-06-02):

Manufacturing, assembly and test procedures for the Athena Turbine v 1.64

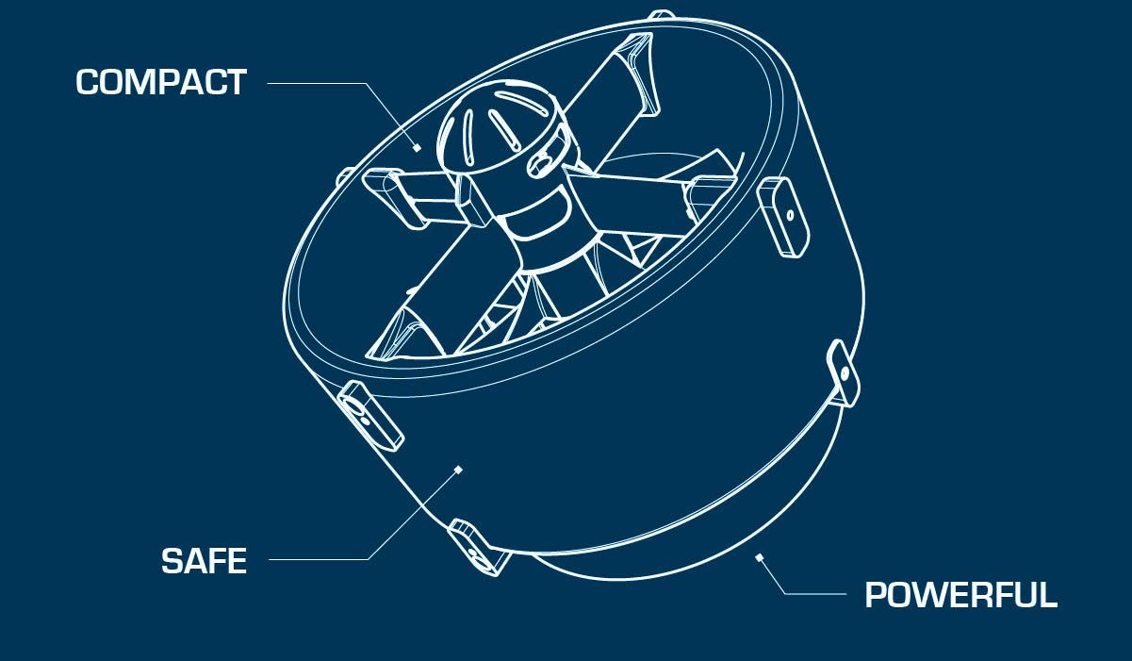
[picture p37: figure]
RÃ©sultat de recherche d'images pour "logo european sustainable propulsion"

# I- Introduction

Before starting the construction of a Athena turbine model, it is important to know which direction of rotation one wants: CW ou CCW. Indeed, despite the fact that the Athena turbines operate with 2 contra rotors, a torque following the axis of the motors is still apparent and is important enough to be taken into account. To determine whether a turbine is designated as CW or CCW, simply look at the inlet rotor from the top of the turbine. If this turns clockwise then the turbine is CW and is CCW if conversely.

It should also be known that the two rotors used in the same turbine are not the same. This must be taken into account when printing the blades, hubs and choosing the right screw (left or right) of the motor axes. So there are a total of four different types of rotors: 1CW inlet/1 CW Outlet And 1CCW inlet/ 1 CCW Outlet. It is easy to recognize the rotor inlet of the rotor outlet and thus the blades and hubs that comprise them: the rotor blades inlet have the thinnest base while for the outlet, the base is thicker.

This Report Describes all the steps that will make it possible to obtain a fully functional Athena model.

# 1. Technical Lexicon

Glossary of the code for the construction stages of the Athena Turbine:

ADJ = Adjustment

ARM = Arm (part)

ASS = Assembly

BLD = Blade (part)

BNCH = Bench

CON = Connector

CRB = Carbon fiber

DRL = Drilling

DRML = Dremel

DRY = Drying

EPXY = Epoxy mix (resin + hardener)

ESC = Electronic Speed Controller

HUB = Hub (part)

LAY = Lay

M3 = M3 threaded rod

MTR = Motor

PARAM = Parameter

PLG = Plug (part)

PNT = Paint

PREP = Preparation

PROD = Production

RTR = Rotor (part)

SHRD = Shroud

SHRDINF = Shroud inferior

SHRDSUP = Shroud superior

SLD = Solder

SND = Sanding

SPR = Spacer bar

STK = Stickers

STRT = Start

TEST = Test

TIE = Tie (collar)

TRB = Turbine Athena

VERIF = Verification

WGT = Weight

WRE = Wire

# II- Repartition du temps

| Opérations | Temps de séchage | Total
Printing parts in 3d | 146 h | / | 146h
Production | 786 min = 13,1h | 51h | 64,1h
Assembly | 347 min = 5,78h | / | 5,78h
Tests | 45 min = 0,75h | / | 0,75h
Painting | 205 min = 3,42h | 48h | 51,42h
| TOTAL = 169,05h | TOTAL = 99h | TOTAL = 268,05h

Total working time to produce a turbine Athena, given for a single worker working 7h per day and assuming that all parts are already printed: 13.1 + 5.78 + 0.75 + 3,42 = 23,05H * = env 3d and a half

* Value Theoretical and Approximate.

In reality and in practice, it will take about 10J between the turbine construction request and Sa Production output For a single worker working 7h per day 5d/7.

# 1. Printing parts and printer settings

Approx time : 146 hours

In order to print the parts correctly and flawlessly, it is essential to follow the following few rules:

-Impressions requiring a high temperature of the nozzle (> 250 °) as for polycarbonate or CPE must be done with a closed enclosure in order to preserve the heat generated by the printing tray. Failure to comply with this rule will create a deformation of the parts or the creation of micro cracks that weaken the workpiece.

-Likewise, and always in the context of impressions requiring high temperatures, it is important to turn off the printing fan (usually the largest of the fans and whose breath is directed towards the nozzle). Be careful not to turn off the extruder fan, which must always remain activated or damage the printer.

-Finally, for parts which always require a high temperature printing, the printing base in contact with the tray exceeds more than 2cmx2cm, use an adhesive sheet (no adhesive spray) to ensure that the first layers Adhere well to the plateau.

Ideal printers for the creation of precise and high-temperature parts such as arms, plugs, Blades: Ultimaker Series

To print the shrouds, a covered creality is recommended.

Printing the shroud :

Top shroud part with integrated plugs CPE on creality = 45 hours

Inside bottom shroud CPE on ultimaker = 25 hours

Outside bottom shroud CPE on creality = 25 hours

Printing arms :

Arm polycarbonate on ultimaker = 14 hours

Printing Blades :

Blade polycarbonate on ultimaker = 2 hours

To be printed one at a time !

Printing hubs :

Hub polycarbonate on ultimaker = 7 hours

Printing plugs :

Plugs black CPE on ultimaker = 5 hours/set (1 set is 2 fitted plugs)

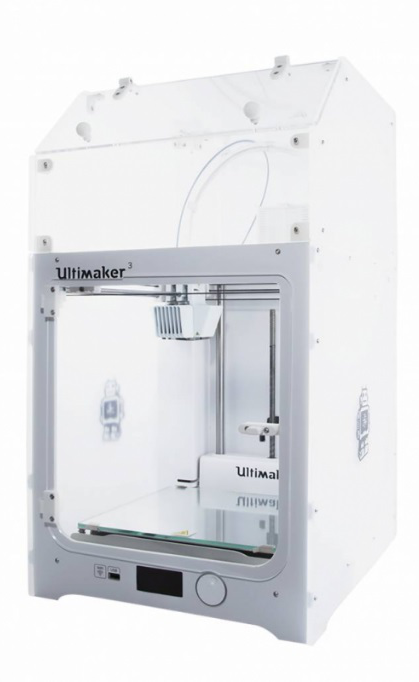
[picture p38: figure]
RÃ©sultat de recherche d'images pour "ultimaker 3 ncover"
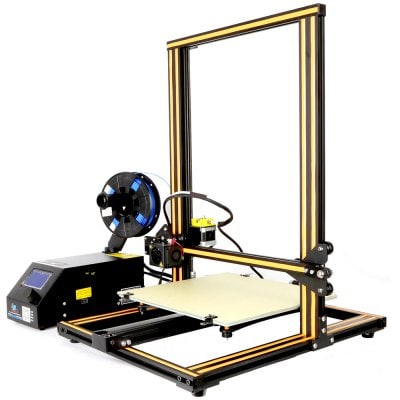
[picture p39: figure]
RÃ©sultat de recherche d'images pour "creality CR-10"

Creality CR-10 Ultimaker 3 with cover

# 1. Manufacture of rotors: PROD-RTR

Approx time : 125 min without drying

Necessary material:

1. 1 Hub Inlet en polycarbonate
2. 1 Hub Outlet en polycarbonate
3. 5 Polycarbonate Inlet Blades
4. 5-Blade Polycarbonate Outlet
5. A drill with diam 6mm drill bit
6. A Dremel with tapered tip
7. One 6mm metal nut with locking with no screws
8. High Glue type Superglue
9. Sanding Paper Grain 240
10. A cutter
11. A hammer
12. An epoxy preparation with a ratio of 5:1 (epoxy resin and hardener)
1. Prep-HUB: At the output of the printer prepare the polycarbonate hubs by removing the printing residues using a cutter. (15 min each)
2. DRL-Hub: Using the drill and the diam 6mm drill bit mounted on it, adjust the diameter of the center hole of the hub in which the 6mm motor axis will pass. To do this, turn the drill in the opposite direction to the bit in order not to twist the hole that composes the hub. Operate delicately. (5 min each)
3. DRML-HUB: Use the Dremel and a tapered tip to skew the edges of the 6mm nut housing to facilitate insertion into the housing. (10 min each)
4. PREP-hub: Insert the nut into the hub. The easiest is to put the nut on a flat surface, then place the hub on the nut and face the housing and then hammer gently to push the nut into its housing. Avoid directly hammering the plastic, for example use a flat wooden wedge between the hammer and the hub. Be careful, the nut must be flat! (5 min each)
5. SND-BLD: At the output of the printer prepare the blades by sanding them lightly with the paper 240 on their surface. Attention they are extremely fragile. Also lightly sand their base until the blade can fit into its housing on the hub. Coat the housing with strong glue before mounting the blade. Fast because the glue dries quickly. (5 min each blade)

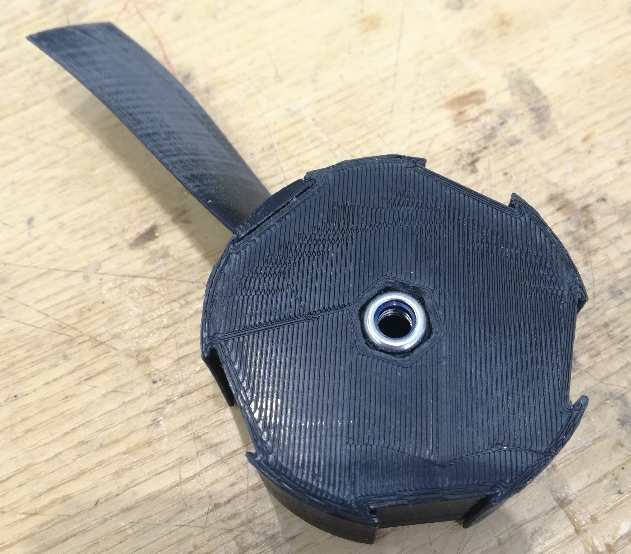
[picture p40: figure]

1. SND-Hub: Once the blades are mounted, sand the hub at the blade feet to level the surface. (10 min each)

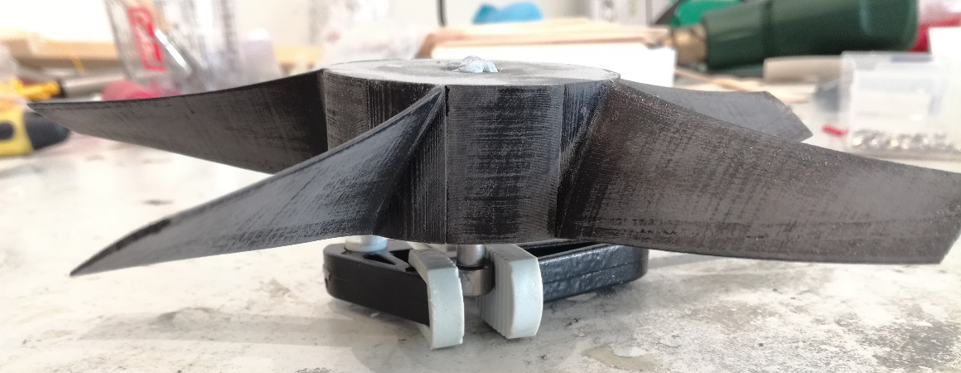
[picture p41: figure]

1- PREP-EPXY : A l’aide d’un étau ou pince étau, mordre une vis de diam 6mm et venir visser partiellement le rotor sur cette vis. De cette manière nous pourrons aisément enduire le rotor d’epoxy sans contact avec les mains.
1. Prep-EPXY: Prepare an epoxy mixture with a ratio of 5:1.

Ex: for 5 units of epoxy resin added, a hardener unit must be mixed

4x5= 20g Epoxy resin → 4g of Hardener and thus total 24g of mixing

20x5= 100g Epoxy resin → 20g of Hardener and therefore total 120g of mixing

Caution, wear gloves when handling with epoxy!

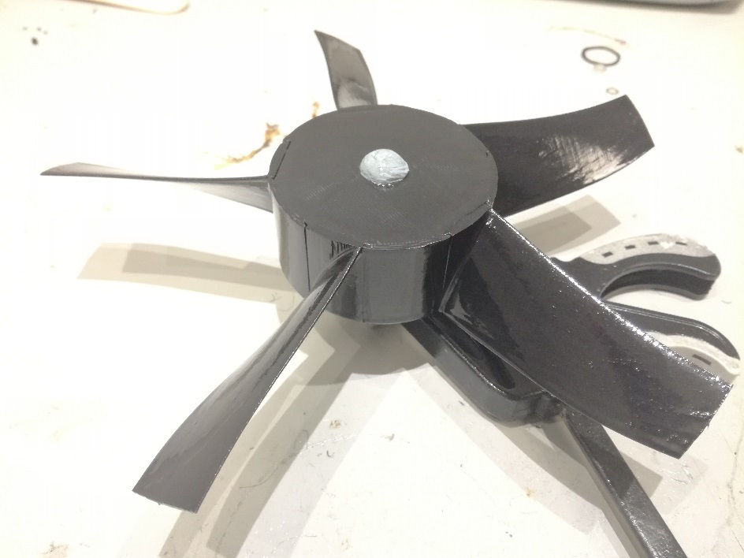
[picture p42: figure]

1. EPXY-RTR: Coat the epoxy rotors with a brush. Do not overdo and exaggerate on the amount of epoxy: soaking the brush only once in the mixture is sufficient to cover a complete rotor. (10 min both)
1. Dry-EPXY: let dry overnight (12h at least)

# 1. Manufacture of ARM sets: PROD-arm

Approx time : 150 min without drying

Necessary material:

1. 2 Polycarbonate-Printed arm assemblies
2. 4 single M3 Nuts without locking
3. 1 dia 3mm threaded rod
4. 1 Fine Clamp
5. 1 cutter
6. Sanding Paper Grain 240
7. An epoxy preparation with a ratio of 5:1 (epoxy resin and hardener)
8. 1 brush
1. Prep-arm: Prepare the arms on their way out of the printer using a cutter to eliminate printing overprints. To remove the 3d-printed media, including the bracket that covers the motor housing, take a rather fine clamp. Fit the clamp into the crevices of the bracket and turn. Repeat the operation until you remove any residual material that has been used to print the workpiece. (15 min each)
2. PREP-arm: Insert the 4 M3 nuts into each unit at the end of the arm. It will be easy enough to insert the nuts in both arms the thick but for the thinner arms, you must first file each of the 6 surfaces of the nut before inserting it. (20 min each)
3. PREP-ARM: Screw the M3 rod into each nut to check if it is not crooked

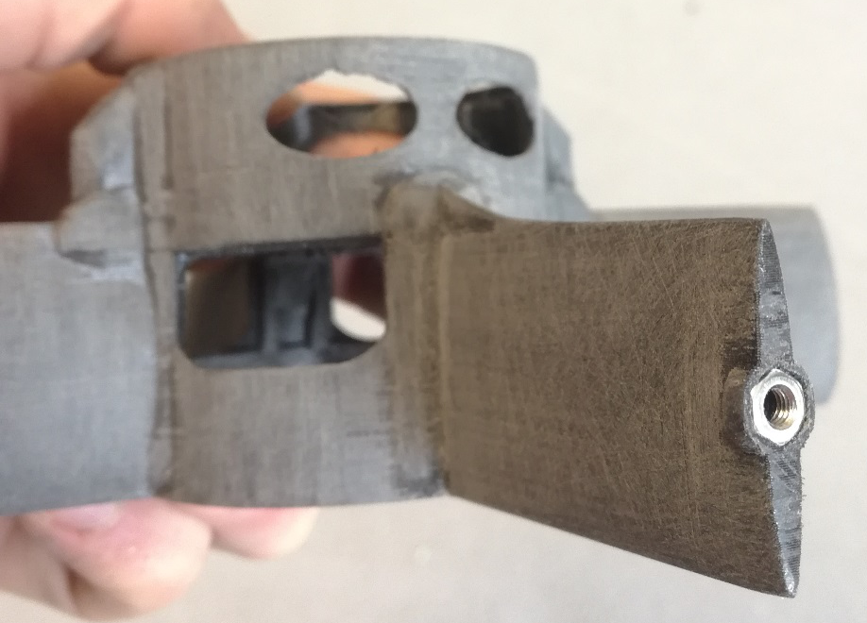
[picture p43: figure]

1- SND-ARM : Sand arms to grain 240 to obtain smooth curves (30 min each)
1. Prep-EPXY: Prepare a support to suspend the arm assemblies when drying the epoxy.
2. Prep-EPXY: Prepare an epoxy mixture with a ratio of 5:1. For this pour 20g of resin for 4g hardener. This quantity is sufficient to coat 2 sets of arms.
3. EPXY-arm: Coat the arm assemblies with care not to insert epoxy into the threads of the nuts. (10 min both)
2- DRY-EPXY Let it dry one night (12 hours at least)

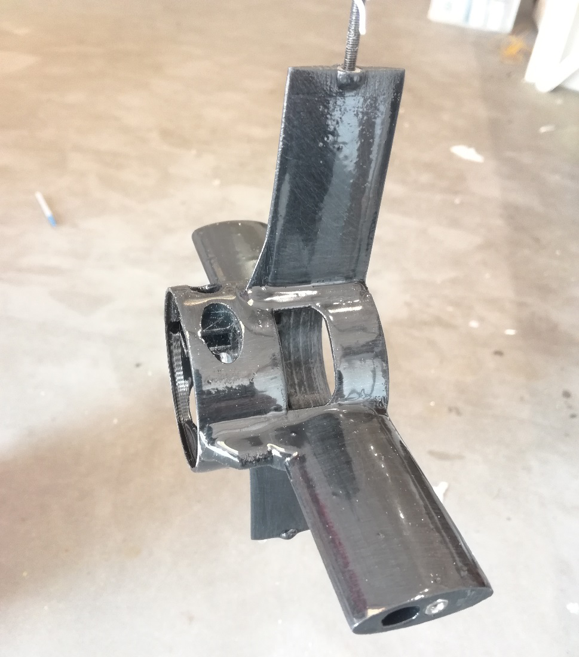
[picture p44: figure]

# 1. Rotor assembly on ARM assemblies: SSA-arm

Approx time : 162 min

Necessary material:

1. 2 Assembled ARM sets
2. 1 rotor Inlet
3. 1 rotor Outlet
4. 2 Caps in polycarbonate to come cover the housing of the ESC
5. 2 MN4010 Tmotor Motors
6. 2 axes motor Tmotor 6mm (Be careful to check the direction of the thread)
7. 14 3mm Hex screw supplied in Tmotor kit
8. 2 ESC castle creation NoBEC
9. 1 Hex Screwdriver 2.5 mm
10. A wire cutter
11. A clip for stripping
12. 1 Soldering iron with tin
13. Heat shrink Sleeve
14. Red and black 14AWG silicone electric wire
15. Medium Strength Loctite (blue color)
1. PREP-MTR: Unpack the Tmotor motor shaft and check its length by placing it against the hub. It must not exceed and if it is the case file it until the desired length is obtained. Attention to the choice of the motor axis, to be chosen according to the direction of rotation of the rotor because some have one step of screw to the left and others one step of screw to the right. (from 2 to 15 min each)
2. PREP-MTR: Unpack the motor and mount its 6mm axis using the 3 fixing screws provided in the kit. Coat them with Loctite beforehand. (5 min each)
3. PREP-arm: Mater The 4 threads present on the arm assembly and which will be used to secure the motor. To do this, take one of the motor fixing screws and screw it gently until the thread is broken. Then unscrew it a bit and press the screw to smooth the hole. Repeat the operation for each of the 4 holes that will support the motor. (10 min each)
4. SSA-RTR-MTR: Screw the rotor onto the motor, being careful not to break the blades. This is one of the most delicate stages of construction. You have to go quietly and with a lot of precaution. (5 min each)

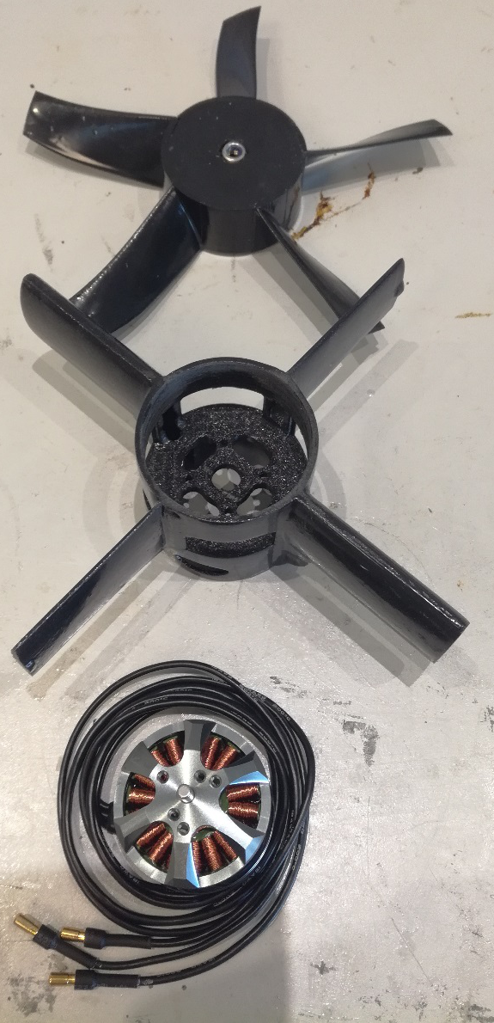
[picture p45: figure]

1- PREP-ESC : Unpack a castle ESC and using a cutting pliers come cut the plastic skirt that covers the 3 wires towards the motor. This will make it easier to insert the ESC into its housing. (2 minutes each)

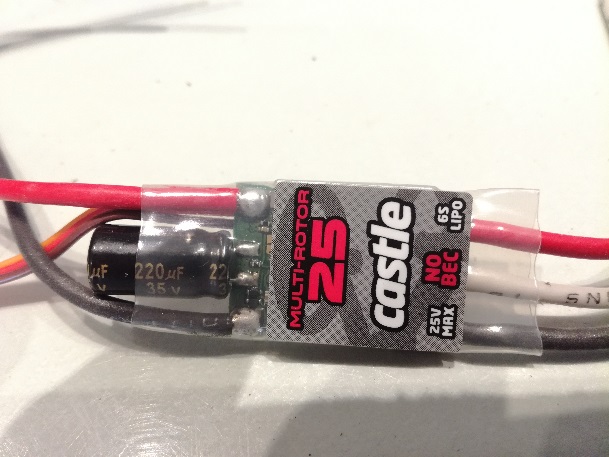
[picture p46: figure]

→

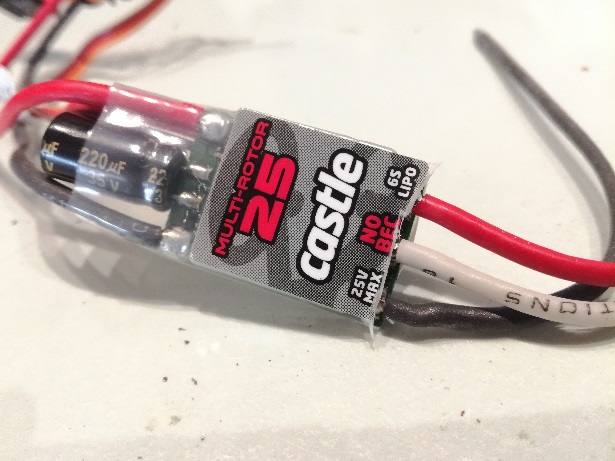
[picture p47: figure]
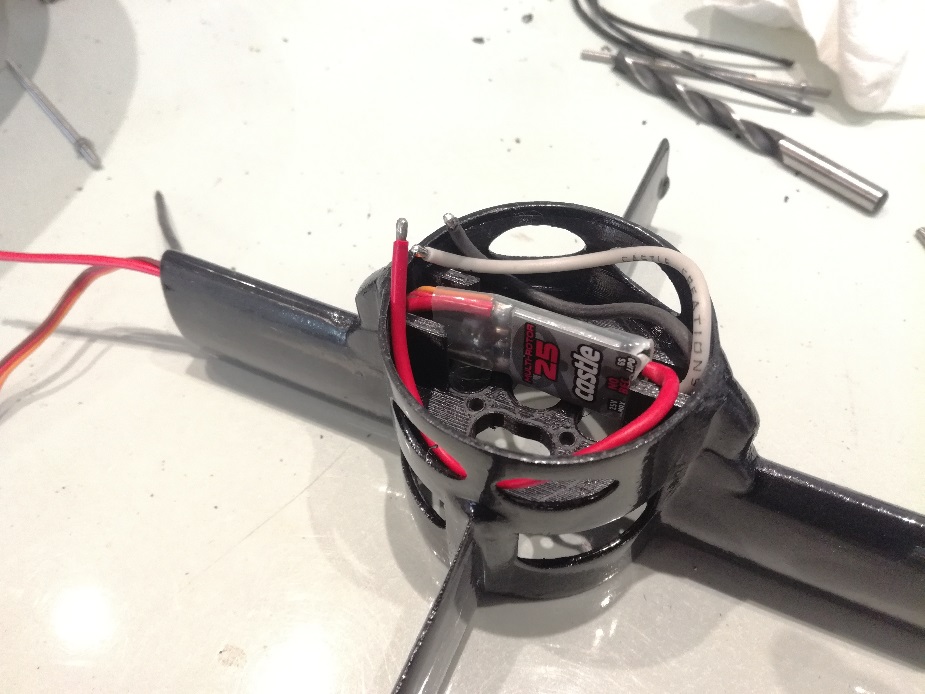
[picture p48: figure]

2- ASS-ESC-ARM : Run the ESC cables (servo jack and wire to battery) into the arm as shown in the picture below. (2 minutes each)
3- ASS-ESC-ARM : Cut the 3 motor wires in half and pass them into the housing provided for them to arrive in the ESC compartment. (5 min each)

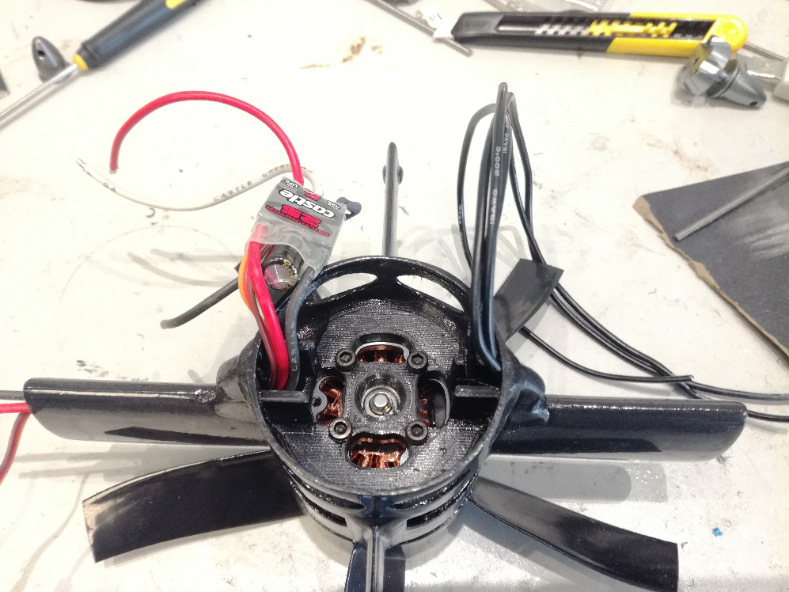
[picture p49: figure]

1. ASS-MTR-ARM : Screw the motor onto its support using the 4 hex M3 screws and apply loctite beforehand. (5 min each)
1. ASS-ESC-MTR : Adjust the motor and ESC wires to the correct length and solder them to the tin. The connection order does not matter. (15 min each)

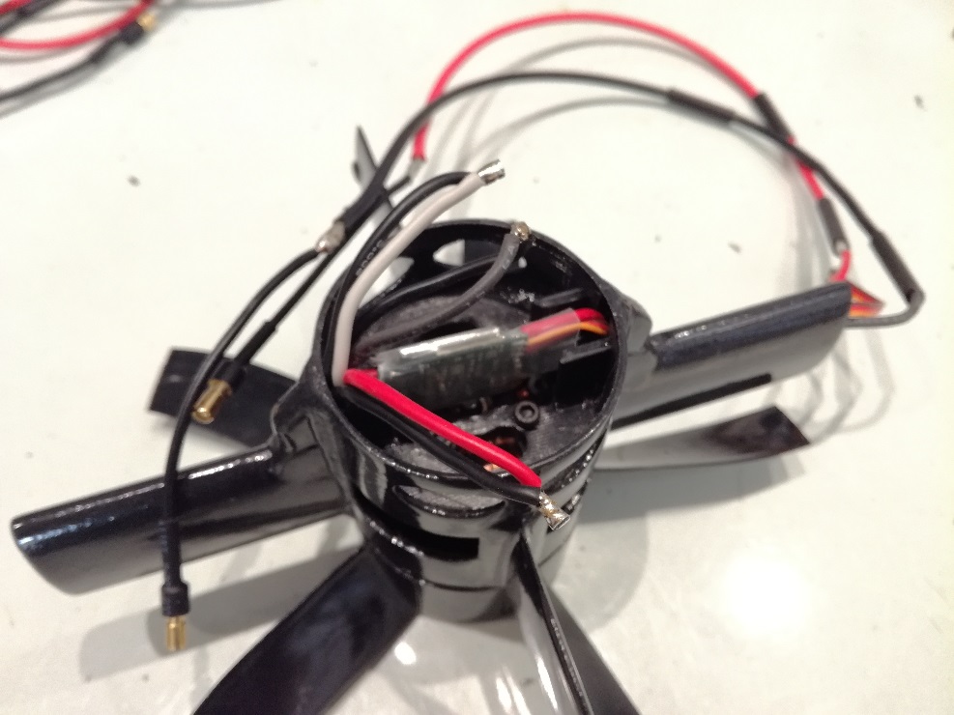
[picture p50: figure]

4- PREP-ESC : Rallonger les fils de l’ESC qui vont vers la batterie de la longueur souhaitée. (15 min each)
1. PREP-ESC/PREP-MTR : Use heat shrink sleeve to mask areas where the wire is visible. (2 minutes each)
5- ASS-ESC-ARM : Press the Polycarbonate caps (hats) on the ESC housing.

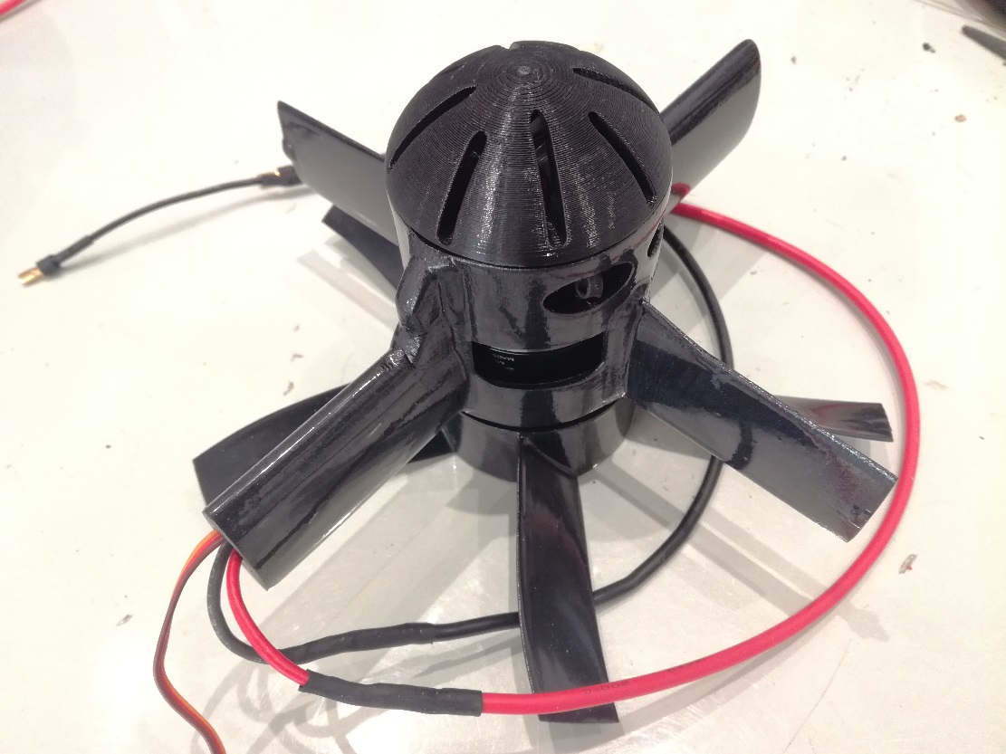
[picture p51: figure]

# III- Fabrication du Shroud : PROD-SHRD

1- TO BE UPDATED WITH NEW PROCEDURE / MAKE A SEPARATE FILE ONLY FOR THE SHROUD

# 1. Finalization of the Athena turbine assembly: SSA-TRB

Approx time : 185 min

Necessary material:

1. 2 Threaded Rods M3
2. 4 Connectors 3mm Male
3. Heat shrink Sleeve
4. A soldering iron with tin
5. A hacksaw
6. A file
7. 8 single M3 nuts without locking
8. High Glue type Superglue
1. PREP-M3: Cut the M3 threaded rods into eight pieces: 4 pieces of length 64mm and 4 pieces of length 85mm. These will be used to maintain the arm-rotor assemblies in the shroud. 1h

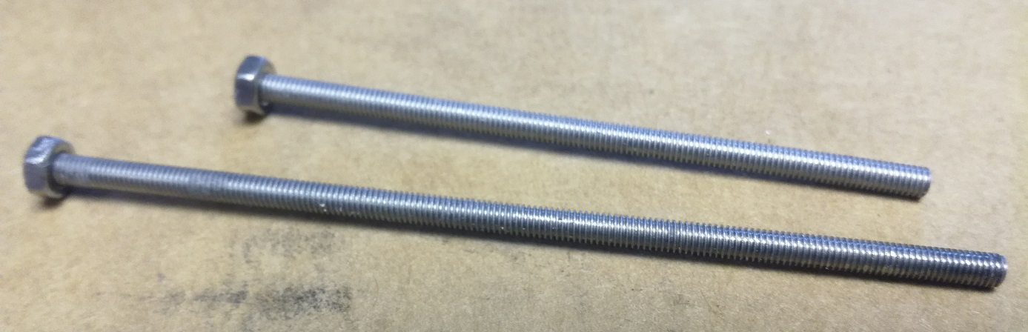
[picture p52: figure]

1- PREP-M3 : Glue a M3 nut to one end of each piece of threaded rod with the superglue. (20 min)
1. ASS-SHRD-ARM : Position the ARM/rotor assembly in the shroud and run the ESC cables through the holes provided for this purpose. (30 min)
2- SLD-CON : Solder the 3mm male connectors to the ESC leads that go in the direction of the battery. (45 min)

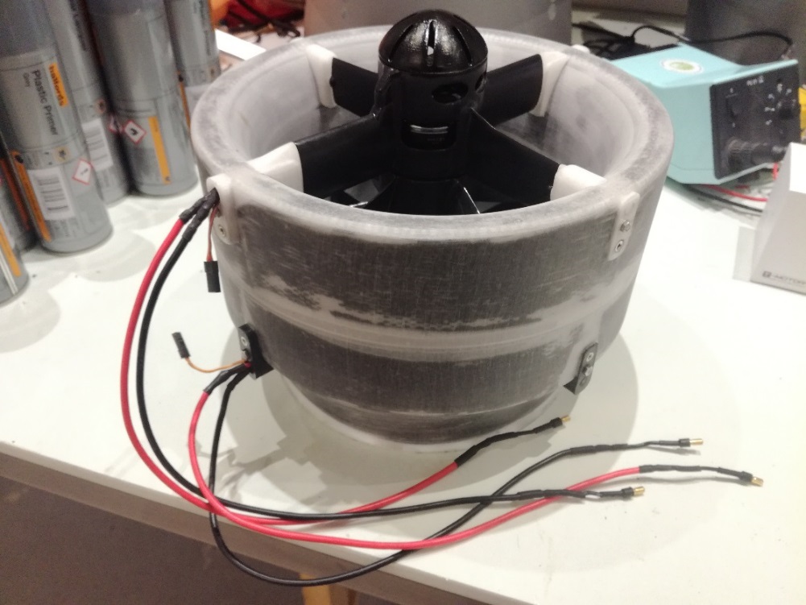
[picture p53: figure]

3- ASS-SHRD-ARM : Attach the arm-rotor assembly to the shroud thanks to the rods previously cut in accordance with the following rule: the rods of length 64mm are intended for the thinnest arms and those of 85mm long to the thickest arms. At this stage the rotors should always be well coaxial and the blades must not touch the inner surface of the shroud. (30 min)

The Athena turbine is now fully assembled. Now up to the test of good functioning

# 1. Test run: Test-TRB

Approx time : 45 min

Necessary material:

1. A voltage supply for each motor and remote controllable.
2. A remotely controllable PWM signal generation system
3. A test bench that allows the turbine to be fixed
4. A force sensor
5. A data acquisition system
6. Neva Aerospace software for displaying collected data
1. SSA-TRB-BNCH: Mount the turbine on the test Bench (5 min)
2. WRE-TRB: Connect the ESC's power cables and signal cables. Attention to Polarity! (5 min)
1- PARAM-ESC: Set ESC with the software and thanks to the transmission via WiFi the voltage delivered by the voltage generators. (10 min)

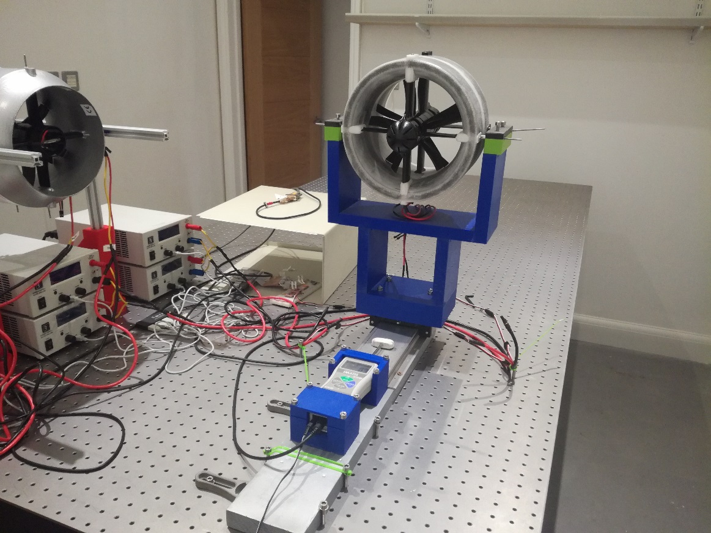
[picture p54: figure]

2- VERIF-WRE : Check that everything is properly plugged in and do a visual inspection of the rotors and shroud to prevent damage to the turbine. (5 min)
1. Leave the test space of the turbine before switching on
1. STRT-Test: Launch the automated turbine test program. (20 min)
2. Observe the results obtained and verify that they correspond to the models already obtained in previous tests with the same turbines.

# 1. Peinture from turbines: PNT-GRT

NEW PROCDURE – External contractor: Prepare turbines for external contractor

TO BE DONE

OLD PROCEDURE: Painting in-house

Approx time : 205 min without drying

Necessary material:

1. 1 Aerosol of Special Grey Plastic Primer (400ml)
2. 1 Spray of special glossy white plastic paint (400ml)
3. 1 Aerosol Clear Gloss varnish
4. 1 sticker Neva Aerospace
5. 1 sticker « this side up »
6. 1 sticker "Do not insert hands in turbine"
7. An insulated part of the wind, with a constant temperature of 20 °c and a humidity not exceeding 50%
1. PREP-NTP: disassemble the turbine rotors so as to keep only the shroud. (15 min)
2. PREP-NTP: Check the surface state of the plastic component of the shroud. This should not have any irregularity, must be clean and well smooth. This step was normally performed in the "SSA-SHRD" section, Step 10, page 21.
3. PREP-NTP: Hide the arm support faces on the plugs with paint tape, and make sure the threads are masked too. (15 min)
4. Prep-NTP: Prepare a flat stand or place the turbine in the area, and in the room where you are going to paint.
5. NTP-SHRD: Follow the instructions on the spray primer. Shake for 3 min and spray on all surfaces of shroud. The first layer should be fine. Wait 15 minutes between each layer. Spray 2 coats evenly on all surfaces. (25 min)
6. Dry-NTP: Allow to dry for 30 min
7. NTP-SHRD: Follow the instructions shown on the paint spray. Shake for 3 min and spray on all surfaces of shroud. The first layer should be fine. Wait 15 minutes between each layer. Spray 3 coats evenly on all surfaces. (45 min)
8. Dry-NTP: Allow to dry at least 24h
1. LAY-STK: Once the paint is dry, glue the stickers in place directly to the paint. (5 min)
2. NTP-SHRD: Follow the instructions shown on the varnish aerosol. Shake for 3 min and spray on all surfaces of shroud. Spray in 1 layer being careful not to over-emphasize in the same place. (10 min)
3. Dry-NTP: let dry 24h
4. SSA-TRB: Raise your Arms in the Shroud (15 min)
5. Test-TRB: Proceed to a bench test again. (45 min)

Example of Athena turbines mounted on the prototype Wohler B Mark III

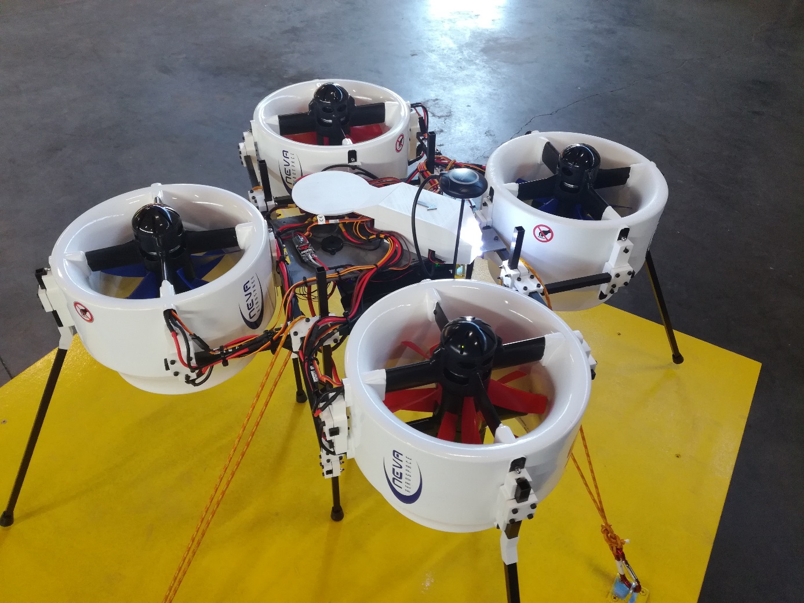
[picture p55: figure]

Confidentiel Neva Aerospace/ESP V1.0

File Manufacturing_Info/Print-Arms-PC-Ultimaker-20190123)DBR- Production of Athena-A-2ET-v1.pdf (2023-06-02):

Robert Vergnes <robert.f.vergnes@gmail.com>

## [NPC-A038 PROTOTYPING OF ATHENA V1.X (2ET) TURBINES] Re: Production of Athena-A-2ET-v1.65

David Brotherton-Ratcliffe (ActiveCollab) <notifications@activecollab.com> | Wed, Jan 23, 2019 at 9:13 PM
Reply-To: notifications-133944@activecollab.com
To: Robert Vergnes <robert.f.vergnes@neva-aero.com>
- Reply above this line to leave a comment -

### New comment posted in: Production of Athena-A-2ET-v1.65

David Brotherton-Ratcliffe 23 Jan 2019
PC (PolyMaker PC-Max) 260C 110C Bed Temp No fan
Layer Height Fine -0.1mm
Outer Wall line width 0.35
Infill Density : Usually 30% should be OK (if you want more strength then 100%) Infill Pattern Grid
Supports: Everywhere
Support Overhang Angle: 80
Support Pattern: Zig Zag (or Grid if supports are falling off in printing) Support Density 20%
Use Towers: NO

Build Plate Adhesion: BRIM is best with the adhesive sheets BRIM WIDTH 15 mm if possible (you will need to have arm at 45 degrees so you have space for this big brim)

or RAFT with Buildtac or glass (with adhesive spray) - but if using raft better to use 5 TOP LAYERS rather than 3.

Always print with door and cover on. Ambient temperature must be around 70-80C. Ultimaker usually struggles to get near 70C...

Older comments

Tomas Valaitis 23 Jan 2019
@David Brotherton-Ratcliffe
Did you could advice to set some specific parameters for Cura slicing for the arm to be printed? Maybe you could upload your Cura settings (profile) you found best for arms?

David Brotherton-Ratcliffe 18 Jan 2019
Here are the latest stl files for v1.64
Note the Arm file is the latest which gives you an extra clearance between the hubs... Top External Plug 4.stl 146.57kb
Top External Plug 2.stl 158.19kb
Top External Plug 1.stl 179.87kb Bottom External Plug 1.stl 198.13kb BEP2.stl 198.13kb
Outlet Hub.stl 262.88kb
Arm.stl 1.99MB
BEP4.stl 317.17kb
BIP4.stl 667.95kb
Top Internal Plug 2.stl 902.04kb Inlet Hub.stl 263.27kb
Cap.stl 2.87MB
Outlet Blade.stl 1.12MB
Inlet Blade.stl 1.13MB
Bottom Internal Plug 3.stl 650.18kb Bottom External Plug 3.stl 246.66kb Bottom Internal Plug 1.stl 766.29kb
Gmail - [NPC-A038 PROTOTYPING OF ATHENA V1.X (2ET) TURBINES] Re: Production of At... | https://mail.google.com/mail/u/0?ik=c024e64846&view=pt&search=all&permmsgid=msg-f:162348...
1 sur 2 | 23/01/2019 à 21:53

BIP2.stl 766.29kb
Top External Plug 3.stl 146.57kb Top Internal Plug 1.stl 0.95MB Top Internal Plug 3.stl 505.94kb Top Internal Plug 4.stl 505.94kb

Robert Vergnes 18 Jan 2019
@David Brotherton-Ratcliffe
the latest I have are those from October :
does the arms and rotor hub are the latest version and blades as well? STL-Files-Date-Athena-1.64.png 219.74kb

Robert Vergnes 18 Jan 2019
@David Brotherton-Ratcliffe

can you post all latest Athena 1.64/1.65 SETP files here: shroud
rotor
arms
blades

we are struggling to find all files back with Tomas

Project: NPC-A038 PROTOTYPING OF ATHENA V1.X (2ET) TURBINES
Task List: Inbox
People in this task: David Brotherton-Ratcliffe, Robert Vergnes, Tal Stokes and Tomas Valaitis

Delivered by ActiveCollab
Getting too many notifications? Unsubscribe from this task or adjust your email settings.
Gmail - [NPC-A038 PROTOTYPING OF ATHENA V1.X (2ET) TURBINES] Re: Production of At... | https://mail.google.com/mail/u/0?ik=c024e64846&view=pt&search=all&permmsgid=msg-f:162348...
2 sur 2 | 23/01/2019 à 21:53

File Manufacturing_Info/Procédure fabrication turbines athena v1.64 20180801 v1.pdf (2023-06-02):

Confidentiel Neva Aerospace/ESP | V1.0

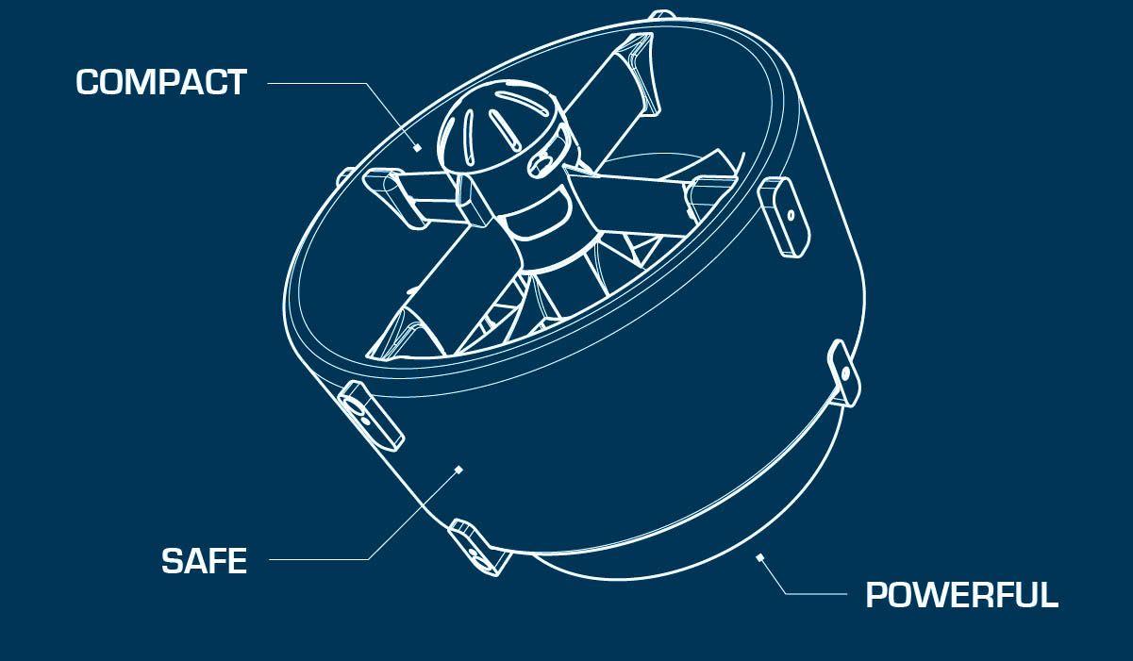
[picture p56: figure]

EDF

# Procédures de fabrication, d’assemblage et de test de la turbine Athena v1.64

## Table des matières

## I- Introduction

Avant de commencer la construction d’un modèle de turbine Athena, il est primordial de savoir quelle sens de rotation on souhaite : CW ou CCW. En effet, malgré le fait que les turbines Athena fonctionnent avec 2 rotors contrarotatifs, un couple suivant l’axe des moteurs est tout de même apparent et est assez important pour être pris en compte. Pour savoir si une turbine est désignée comme CW ou CCW, il suffit de regarder le rotor inlet par le haut de la turbine. Si celui-ci tourne dans le sens horaire alors la turbine est CW et est CCW si inversement.

Il faut également savoir que les 2 rotors utilisés dans une même turbine ne sont pas les mêmes. Il faudra tenir compte de cela lors de l’impression des pales, des hubs et choisir le bon pas de vis (a gauche ou à droite) des axes moteur. Il y a donc au total 4 types de rotors différents : 1CW inlet/1 CW Outlet et 1CCW inlet/ 1 CCW Outlet. Il est facile de reconnaître le rotor inlet du rotor outlet et ainsi donc les pales et hubs qui les composent : Les pales du rotor inlet ont la base la plus fine tandis que pour l’outlet, la base est plus épaisse.

Ce rapport décrit toutes les étapes qui permettront d’obtenir un modèle Athena pleinement fonctionnel.

## II- Lexique technique

Lexique du code des étapes de la construction de la turbine Athéna :

ADJ = Adjustment

ARM = Arm (part)

ASS = Assembly

BLD = Blade (part)

BNCH = Bench

CON = Connector

CRB = Carbon fiber

DRL = Drilling

DRML = Dremel

DRY = Drying

EPXY = Epoxy mix (resin + hardener)

ESC = Electronic Speed Controller

HUB = Hub (part)

LAY = Lay

M3 = M3 threaded rod

MTR = Motor

PARAM = Parameter

PLG = Plug (part)

PNT = Paint

PREP = Preparation

PROD = Production

RTR = Rotor (part)

SHRD = Shroud

SHRDINF = Shroud inferior

SHRDSUP = Shroud superior

SLD = Solder

SND = Sanding

SPR = Spacer bar

STK = Stickers

STRT = Start

TEST = Test

TIE = Tie (collar)

TRB = Turbine Athena

VERIF = Verification

WGT = Weight

WRE = Wire

III- | Repartition du temps
| Opérations | Temps de séchage | Total
Impression des pieces en 3D | 146 h | / | 146h
Production | 786 min = 13,1h | 51h | 64,1h
Assemblage | 347 min = 5,78h | / | 5,78h
Tests | 45 min = 0,75h | / | 0,75h
Peinture | 205 min = 3,42h | 48h | 51,42h
| TOTAL = 169,05h | TOTAL = 99h | TOTAL = 268,05h

Temps total de travail effectif pour produire une turbine Athéna, donné pour un seul ouvrier travaillant 7h par jour et en faisant l’hypothèse que toutes les pièces sont déjà imprimées : 13,1 + 5,78 + 0,75 + 3,42 = 23,05h* = env 3j et demi
*Valeur théorique et approximative.

En réalité et en pratique, il faudra compter environ 10j entre la demande de construction de la turbine et sa sortie de production pour un seul ouvrier travaillant 7h par jour 5j/7.

## IV- Impression des pièces et réglages des imprimantes

Approx time : 146 hours

Afin d’imprimer les pièces correctement et sans défaut, il est primordial de respecter les quelques règles suivantes :

- Les impressions nécessitant une haute température de la buse (>250°) comme pour le Polycarbonate ou le CPE doivent se faire impérativement à enceinte fermée afin de conserver la chaleur générée par le plateau d’impression. Le non-respect de cette règle entrainera la déformation des pièces ou encore la création de micro fissures fragilisant la pièce.
- De même, et toujours dans le cadre des impressions nécessitant de hautes températures, il est important de désactiver le ventilateur d’impression (généralement le plus gros des ventilateurs et dont le souffle est dirigé vers la buse). Attention à ne pas désactiver le ventilateur de l’extruder, qui lui doit toujours rester activé sous peine d’endommager l’imprimante.
- Enfin, pour les pièces nécessitant toujours une impression avec haute température, dont la base d’impression en contact avec le plateau dépasse plus de 2cmx2cm, utiliser une feuille adhésive (pas de spray adhésif) afin de s’assurer que les premières couches adhèrent bien au plateau.

Imprimantes idéales pour la création de pièces précises et à haute température comme les bras, plugs, pales : séries Ultimaker

Pour imprimer les shrouds, une creality couverte est conseillée.

Impression du shroud :

Top shroud part with integrated plugs CPE on creality = 45 hours

Inside bottom shroud CPE on ultimaker = 25 hours

Outside bottom shroud CPE on creality = 25 hours

Impression des bras :

Arm polycarbonate on ultimaker = 14 hours

Impression des pales :

Blade polycarbonate on ultimaker = 2 hours

To be printed one at a time !

Impression des hubs :

Hub polycarbonate on ultimaker = 7 hours

Impression des plugs :

Plugs black CPE on ultimaker = 5 hours/set (1 set is 2 fitted plugs)

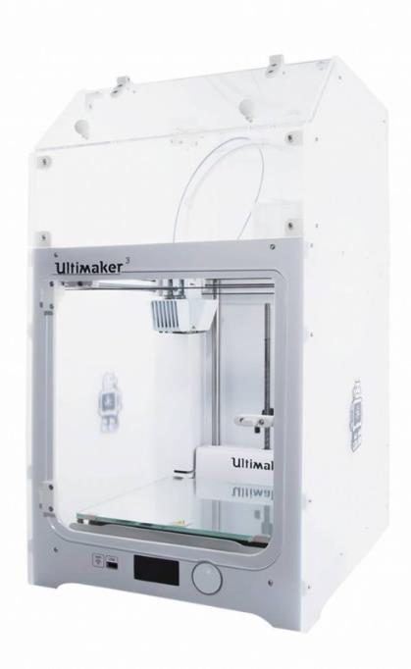
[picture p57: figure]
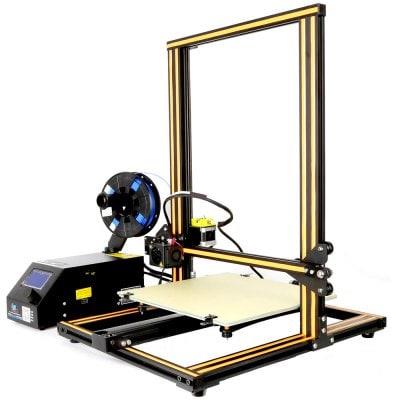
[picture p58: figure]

Creality CR-10 | Ultimaker 3 with cover

## V- Fabrication des rotors : PROD-RTR

Approx time : 125 min without drying
Matériel nécessaire :
- 1 Hub Inlet en polycarbonate
- 1 Hub Outlet en polycarbonate
- 5 pales Inlet en polycarbonate
- 5 pales Outlet en polycarbonate
- Une perceuse avec mèche de diam 6mm
- Une dremel avec embout conique
- Un écrou métal de 6mm avec Nylstop avec pas de vis à
- Colle forte type superglue
- Papier à poncer grain 240
- Un cutter
- Un marteau
- Une préparation Epoxy avec un ratio 5 :1 (résine epoxy et durcisseur)

1- PREP-HUB : A la sortie de l’imprimante préparer les hubs en polycarbonate en les débarrassant des résidus d’impression à l’aide d’un cutter. (15 min each)

2- DRL-HUB : A l’aide la perceuse et de la mèche de diam 6mm montée dessus, ajuster le diamètre du trou central du hub dans lequel passera l’axe moteur de 6mm. Pour cela faire tourner la perceuse dans le sens inverse à celui de la mèche afin de ne pas vriller le trou qui compose le hub. Opérer délicatement. (5 min each)

3- DRML-HUB : A l’aide de la dremel et d’un embout conique, venir biaiser les bords du logement de l’écrou de 6mm afin de faciliter son insertion dans son logement. (10 min each)

4- PREP-HUB : Insérer l’écrou dans le hub. Le plus facile est de poser l’écrou sur une surface plate, puis de poser le hub sur l’écrou et face à son logement et ensuite venir marteler délicatement pour enfoncer l’écrou dans son logement. Eviter de marteler directement le plastique, utiliser par exemple une cale plate en bois entre le marteau et le hub. Attention, l’écrou doit être bien à plat ! (5 min each)

5- SND-BLD : A la sortie de l’imprimante préparer les pales en les ponçant légèrement avec le papier 240 sur leur surface. Attention elles sont extrêmement fragiles. Poncer également légèrement leur base jusqu’à ce que la pale puisse s’insérer dans son logement sur le hub. Enduire le logement de colle forte avant d’y monter la pale. Faire vite car la colle sèche rapidement. (5 min each blade)

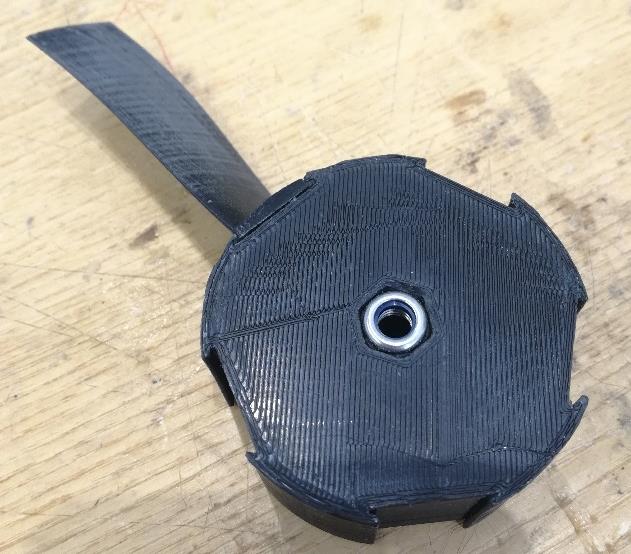
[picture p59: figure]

6- SND-HUB : Les pales une fois montées, poncer le hub au niveau des pieds de pale pour égaliser la surface. (10 min each)

7- PREP-EPXY : A l’aide d’un étau ou pince étau, mordre une vis de diam 6mm et venir visser partiellement le rotor sur cette vis. De cette manière nous pourrons aisément enduire le rotor d’epoxy sans contact avec les mains.

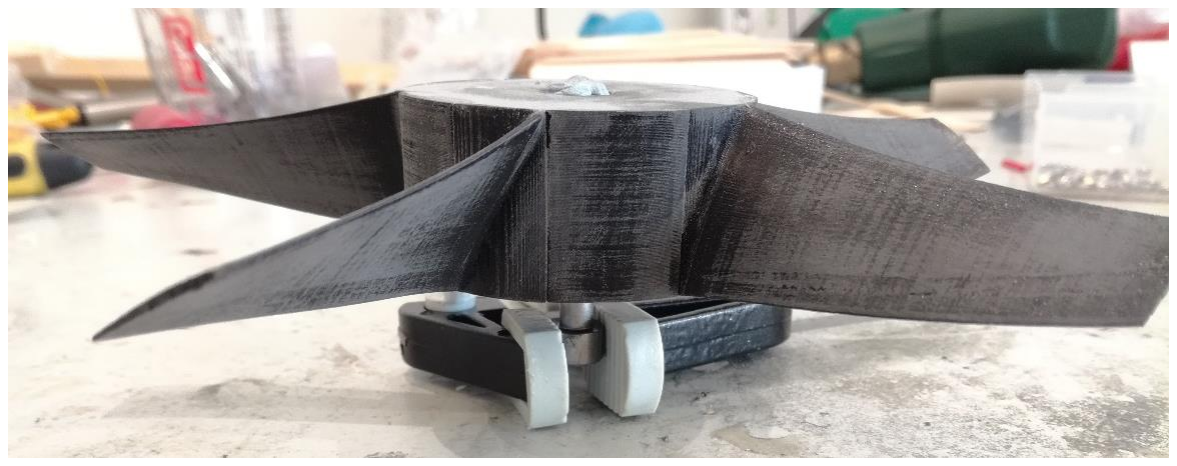
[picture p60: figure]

8- PREP-EPXY : Préparer un mélange d’epoxy avec un ratio de 5 :1.
Ex : Pour 5 unités de résine epoxy ajoutée, il faudra mélanger une unité de durcisseur 4x5=20g de résine epoxy → 4g de durcisseur et donc au total 24g de mélange 20x5=100g de résine epoxy → 20g de durcisseur et donc au total 120g de mélange Attention, porter des gants lors des manipulations avec l’epoxy !

9- EPXY-RTR : Enduire les rotors d’epoxy à l’aide d’un pinceau. Ne pas trop insister et ne pas exagérer sur la quantité d’epoxy : bien Tremper le pinceau une seule fois dans le mélange suffit pour couvrir un rotor complet. (10 min both)

10- DRY-EPXY : Laisser sécher une nuit (12h at least)

## VI- Fabrication des ensembles bras : PROD-ARM

Approx time : 150 min without drying
Matériel nécessaire :
- 2 ensembles bras imprimés en polycarbonate
- 4 écrous M3 simples sans Nylstop
- 1 tige filetée de diam 3mm
- 1 pince fine
- 1 cutter
- Papier à poncer grain 240
- Une préparation Epoxy avec un ratio 5 :1 (résine epoxy et durcisseur)
- 1 pinceau

1- PREP-ARM : Préparer les bras à leur sortie de l’imprimante à l’aide d’un cutter pour éliminer les surplus d’impression. Pour retirer les supports imprimés en 3D, notamment le support qui couvre le logement du moteur, prendre une pince assez fine. Planter la pince dans les interstices du support et tourner. Répéter l’opération jusqu’à enlever tout résidu de support ayant servi à l’impression de la pièce. (15 min each)

2- PREP-ARM : Insérer les 4 écrous M3 dans chaque logement en bout de bras. Il sera assez facile d’insérer les écrous dans les 2 bras les épais mais pour les bras les plus fin, il faudra préalablement limer chacune des 6 surfaces de l’écrou avant de l’insérer. (20 min each)

3- PREP-ARM : Visser la tige M3 dans chaque écrou afin de vérifier si celui-ci n’est pas de travers

4- SND-ARM : Poncer les bras au grain 240 pour obtenir des courbes lisses (30 min each)

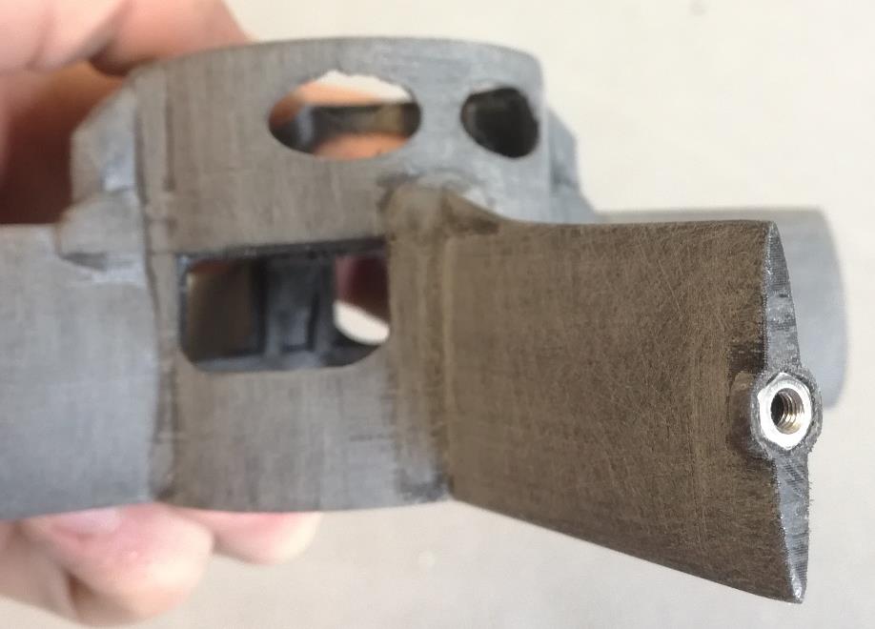
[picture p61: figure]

5- PREP-EPXY : Préparer un support pour pouvoir suspendre les ensembles de bras lors du séchage de l’epoxy.

6- PREP-EPXY : Préparer un mélange d’epoxy avec un ratio de 5 :1. Pour cela verser 20g de résine pour 4g de durcisseur. Cette quantité est suffisante pour enduire 2 ensembles de bras.

7- EPXY-ARM : Enduire les ensembles de bras en faisant attention de ne pas insérer d’epoxy dans le filetage des écrous. (10 min both)

8- DRY-EPXY Laisser sécher une nuit (12 hours at least)

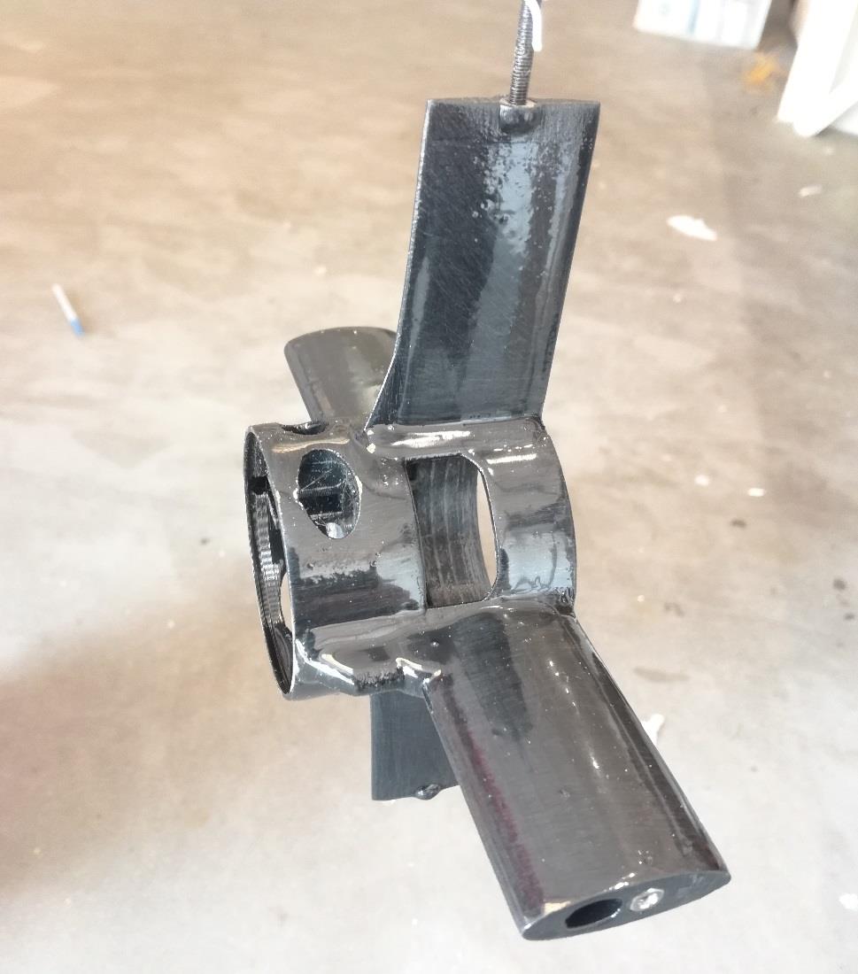
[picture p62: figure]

## VII- Assemblage rotors sur les ensembles bras : ASS-ARM

Approx time : 162 min
Matériel nécessaire :
- 2 ensembles bras montés
- 1 rotor Inlet
- 1 rotor Outlet
- 2 Caps en polycarbonate pour venir couvrir le logement de l’ESC
- 2 moteurs Tmotor MN4010
- 2 axes moteur Tmotor 6mm (attention à vérifier le sens du filetage)
- 14 vis hexa de 3mm fournies dans le kit Tmotor
- 2 ESC castle creation NoBEC
- 1 tournevis hexagonal 2,5mm
- Une pince coupe fil
- Une pince pour dénuder
- 1 fer à souder avec étain
- Gaine thermo rétractable
- Du fil électrique silicone 14AWG rouge et noir
- Loctite de force moyenne (couleur bleu)

1- PREP-MTR : Déballer l’axe moteur Tmotor et vérifier sa longueur en le posant contre le hub. Il ne doit pas dépasser et si c’est le cas le limer jusqu’à obtenir la longueur souhaitée. Attention au choix de l’axe moteur, à choisir en fonction du sens de rotation du rotor car certains ont un pas de vis à gauche et d’autres un pas de vis à droite. (from 2 to 15 min each)

2- PREP-MTR : Déballer le moteur et monter son axe de 6mm a l’aide des 3 vis de fixation fournies dans le kit. Les enduire de loctite au préalable. (5 min each)

3- PREP-ARM : Mater les 4 filetages présents sur l’ensemble bras et qui serviront à venir fixer le moteur. Pour cela prendre une des vis de fixation du moteur et la visser délicatement jusqu’à rupture du filetage. Ensuite la dévisser un peu et appuyer fort sur la vis afin de lisser le trou. Répéter l’opération pour chacun des 4 perçages qui supporteront le moteur. (10 min each)

4- ASS-RTR-MTR : Visser le rotor sur le moteur en faisant très attention de ne pas casser les pales. Cette étape est une des plus délicates de la construction. Il faut y aller calmement et avec beaucoup de précaution. (5 min each)

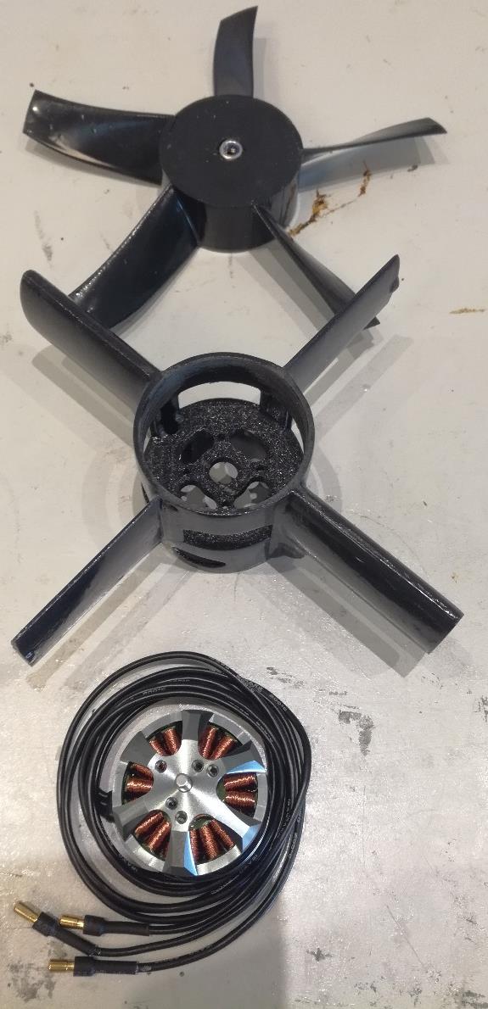
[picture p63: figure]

5- PREP-ESC : Déballer un ESC castle et à l’aide d’une pince coupante venir couper la jupe en plastique qui recouvre les 3 fils en direction du moteur. Cela permettra d’insérer plus facilement l’ESC dans son logement. (2 minutes each)

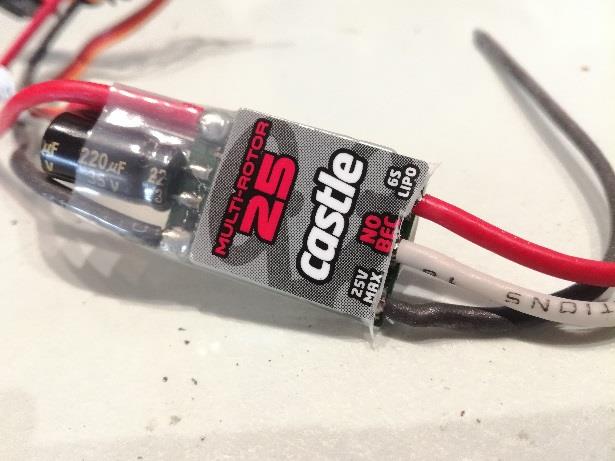
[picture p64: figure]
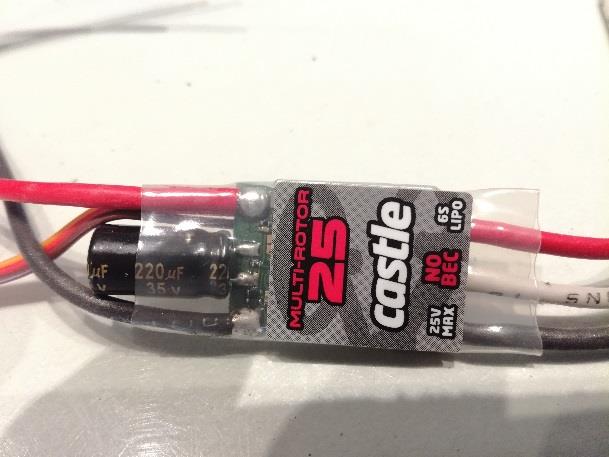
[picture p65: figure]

→

6- ASS-ESC-ARM : Faire passer les câbles de l’ESC (prise servo et fils vers batterie) dans le bras comme montré dans la photo ci-dessous. (2 minutes each)

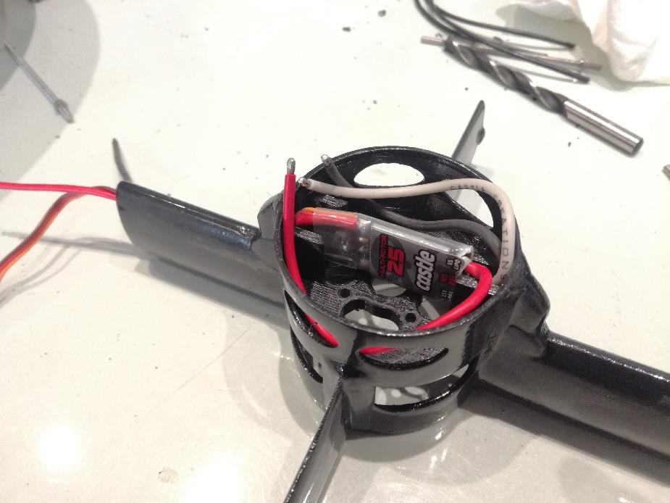
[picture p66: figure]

7- ASS-ESC-ARM : Couper de moitié les 3 fils du moteur et les faire passer dans le logement prévu à cet effet pour qu’ils arrivent dans le compartiment de l’ESC. (5 min each)

8- ASS-MTR-ARM : Visser le moteur sur son support à l’aide des 4 vis hexa M3 et les enduire de loctite au préalable. (5 min each)

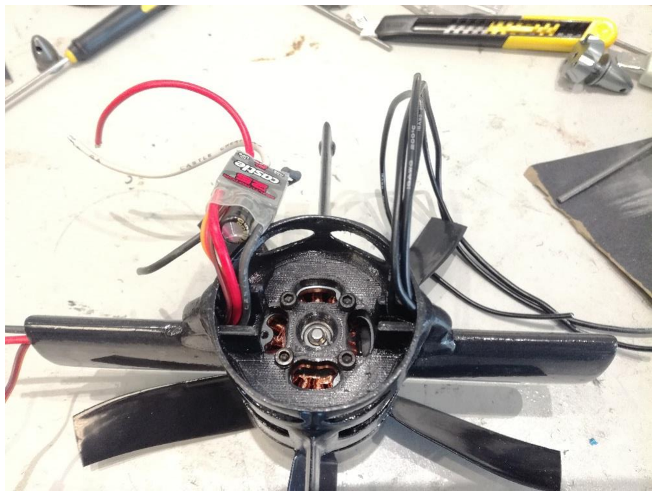
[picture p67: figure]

9- ASS-ESC-MTR : Ajuster les fils moteurs et ESC à la bonne longueur et les souder à l’étain. L’ordre de connexion n’a pas d’importance. (15 min each)

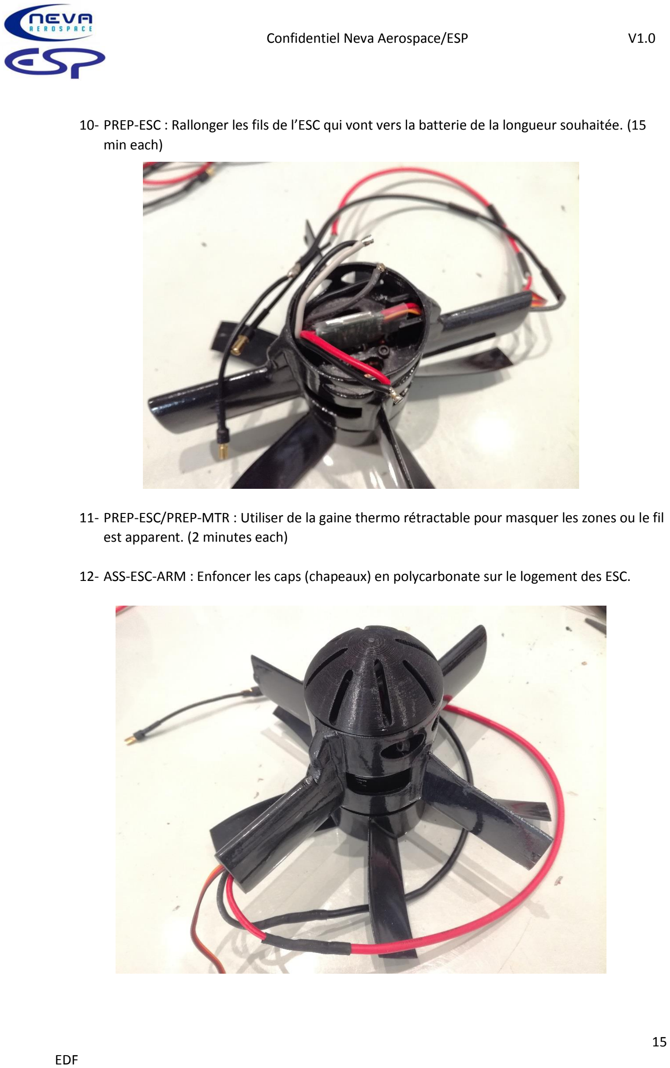
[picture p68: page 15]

10- PREP-ESC : Rallonger les fils de l’ESC qui vont vers la batterie de la longueur souhaitée. (15 min each)

11- PREP-ESC/PREP-MTR : Utiliser de la gaine thermo rétractable pour masquer les zones ou le fil est apparent. (2 minutes each)

12- ASS-ESC-ARM : Enfoncer les caps (chapeaux) en polycarbonate sur le logement des ESC.

## VIII- Fabrication du Shroud : PROD-SHRD

Approx total time without drying : 511 min = about 8h30min Matériel nécessaire :

- Partie supérieure du shroud
- Partie inférieur et extérieur du shroud
- Partie inférieur et intérieur du shroud
- Un anneau de jointure qui viendra centrer les parties inférieurs et supérieures.
- Set de 4 paires de connecteurs (plugs) en polycarbonate
- Rouleaux de fibre de carbone de largeur 10 cm et 2,5 cm.
- Une préparation epoxy avec un ratio 5 :1
- Une préparation epoxy achetée en tube
- 2 ou 3 pinceaux
- Des sticks en bois type « bâtonnets de glace »
- Un cutter
- Papier à poncer grain 60, 120, 240, 350, 400
- 8 Entretoises hexagonales M3 de longueur 25mm
- 1 lime biseautée
- 1 lime ronde
- 1 perceuse ou dremel avec un embout rond de ponçage de diamètre 10mm
- Tige filetée M3
- Colle forte type superglue
- Plusieurs Rilsans
- Un poids de 8-10kg

### Partie supérieure : SHRDSUP

Approx time without drying: 25 min

1- PREP-SHRDSUP : Préparer à sa sortie de l’imprimante la pièce supérieure du shroud. A l’aide d’un cutter enlever tous les résidus d’impression. (5 min)

2- PREP-CRB : Couper des bandes de fibre de carbone de manière à remplir l’espace interne de la pièce constituant le shroud supérieur. (5 min)

3- PREP-EPXY : Préparer un mélange résine epoxy + durcisseur

4- EPXY-SHRDSUP : Enduire d’epoxy l’intérieur du shroud supérieur à l’aide du pinceau et apposer les bandes de fibre de carbone. Passer ensuite une nouvelle couche d’epoxy au pinceau sur la fibre. (15 min)

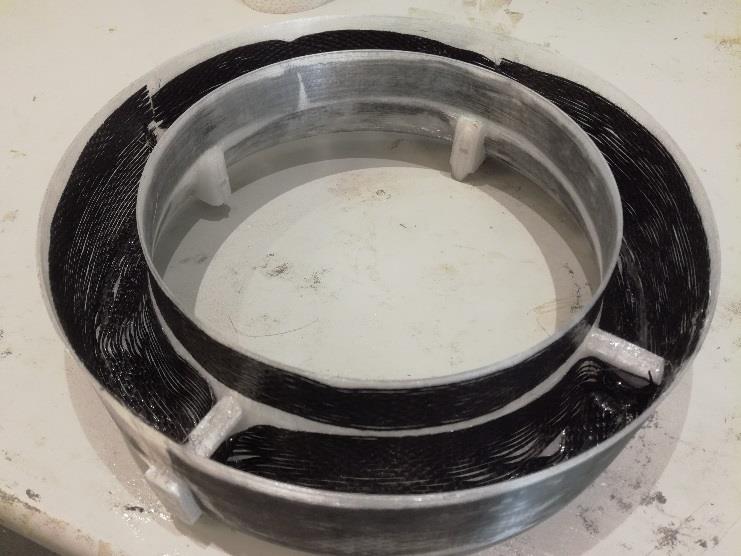
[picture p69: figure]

5- DRY-SHRDSUP : Laisser sécher une nuit. (at least 12 hours)

### Partie inférieure : SHRDINF

Approx time : 170 min

1- PREP-PLG : Commencer par préparer les pièces imprimées en 3D. A l’aide du cutter retirer les résidus d’impression indésirables et vérifier que les plugs en polycarbonate se connectent parfaitement. Attention à avoir le bon set de plugs (4 paires non identiques : les 2 paires qui supporteront les bras fins sur lesquels reposent les rotors sont identiques. En revanche celles qui supporteront les bras épais sont différentes, une des paires ayant un trou creux permettant le passage des câbles de l’ESC). (1h30 min)

2- PREP-SHRDINF : Préparer les 2 pièces composant la partie inférieure de la même manière, à l’aide du cutter. (10 min)

3- DRML-PLG : Avec une dremel ou perceuse et une lime ronde agrandir les trous de passage des plugs. (20 min)

4- ASS-PLG-SHRDINF : Monter les plugs dans les 2 pièces composant le shroud inférieur, permettant ainsi de les maintenir ensemble. (10 min)

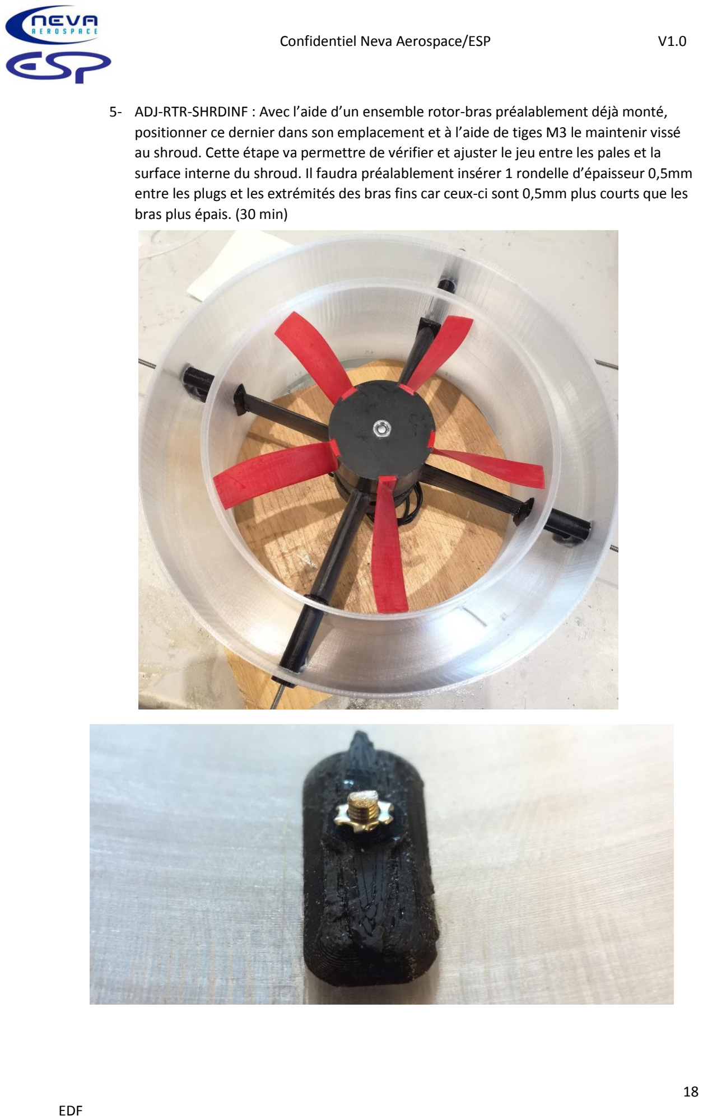
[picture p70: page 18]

5- ADJ-RTR-SHRDINF : Avec l’aide d’un ensemble rotor-bras préalablement déjà monté, positionner ce dernier dans son emplacement et à l’aide de tiges M3 le maintenir vissé au shroud. Cette étape va permettre de vérifier et ajuster le jeu entre les pales et la surface interne du shroud. Il faudra préalablement insérer 1 rondelle d’épaisseur 0,5mm entre les plugs et les extrémités des bras fins car ceux-ci sont 0,5mm plus courts que les bras plus épais. (30 min)

6- ADJ-SHRDINF-SHRDSUP : Monter temporairement l’anneau de jointure et la partie haute du shroud afin toujours de vérifier le bon centrage du rotor. (10 min)

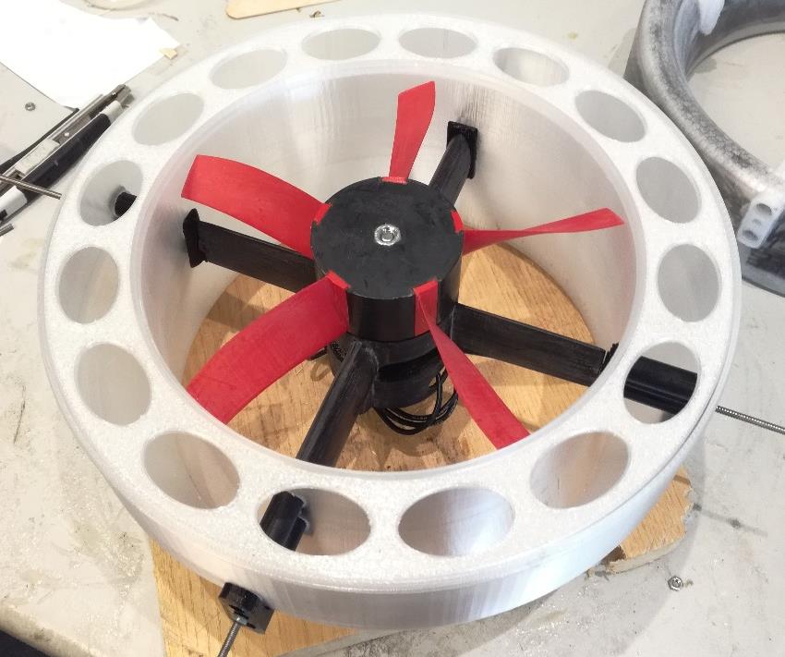
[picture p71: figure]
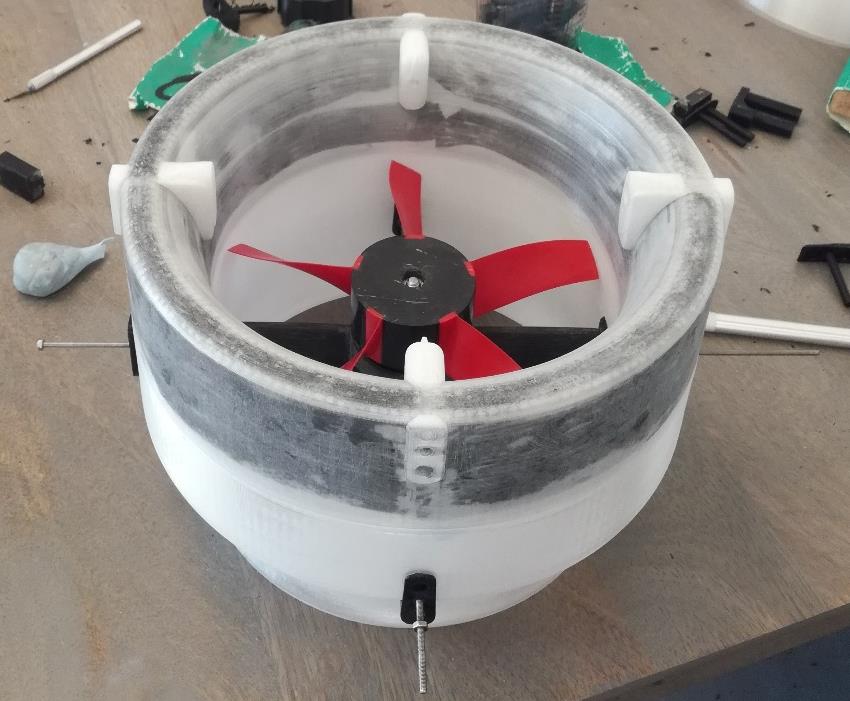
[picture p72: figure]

6- ADJ-SHRDINF-SHRDSUP : Enlever la partie haute du shroud et l’anneau de jointure mais laisser l’ensemble rotor-bras monté.

NB : Le ponçage des 2 parties se fera plus tard, une fois celles-ci assemblées. Cf étape 9 de la partie « Assemblage partie haute et partie basse »

### Assemblage de la partie haute et de la partie basse : ASS-SHRD

Approx time without drying : 316 min

1- PREP-CRB : Couper des bandes de fibre de carbone de manière à remplir tout l’espace interne du shroud inférieur. (10 min)

2- PREP-TIE : Préparer 2 colliers un peu plus grand que le diamètre extérieur du shroud faits avec des rilsans (10 min)

3- PREP-EPXY : Préparer un mélange résine epoxy + durcisseur

4- EPXY-SHRDINF : Enduire d’epoxy l’intérieur du shroud inférieur à l’aide du pinceau et apposer les bandes de fibre de carbone. Passer ensuite une nouvelle couche d’epoxy au pinceau sur la fibre. Une fois terminé, immédiatement monter et centrer l’anneau de jointure. Enduire d’epoxy les bords du shroud supérieur et joindre les 2 parties en faisant attention de mettre sur le même axe vertical les trous de passage de câbles des ESC. (pour cela insérer une tige M3 dans chacun des trous de fixation de la turbine qui sont sur le même axe et avec une équerre venir aligner verticalement ces 2 tiges). Cette étape est complexe car il faut faire toutes les manipulations décrites ci-dessus rapidement puisque l’epoxy commence à durcir au bout de 20 min. (30 min)

5- TIE-SHRD : Placer les colliers de Rilsans autour du shroud et insérer entre les deux parties un maximum de languettes en bois afin de venir faire pression sur les parois. (10 min)

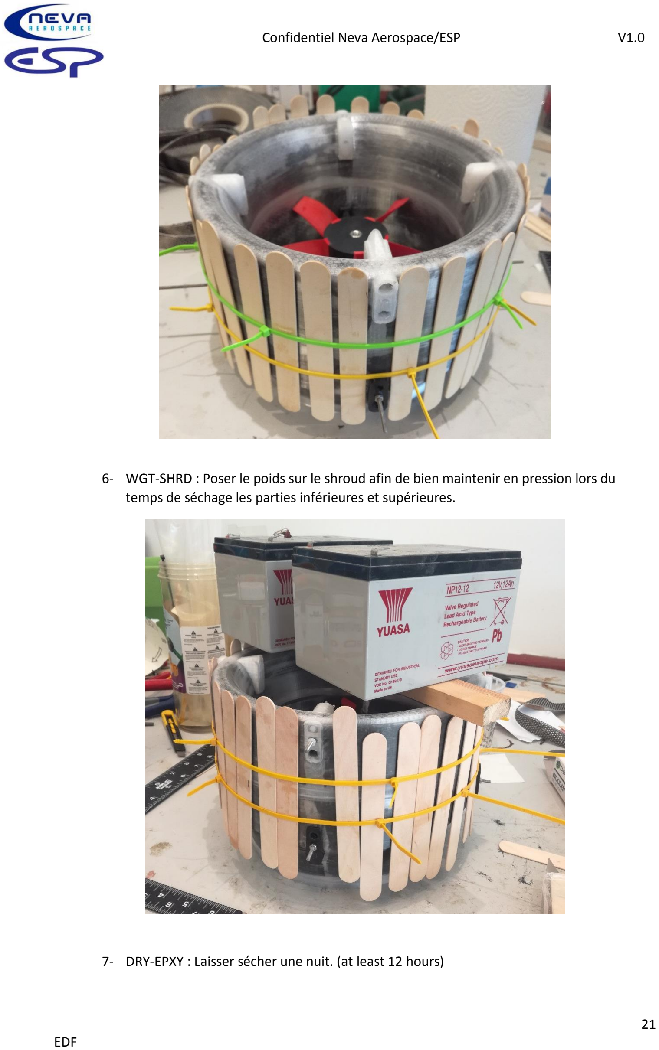
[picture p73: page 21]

6- WGT-SHRD : Poser le poids sur le shroud afin de bien maintenir en pression lors du temps de séchage les parties inférieures et supérieures.

7- DRY-EPXY : Laisser sécher une nuit. (at least 12 hours)

8- PREP-SHRD : Une fois sec retirer le poids, les rilsans et les languettes en bois puis avec une lame de cutter racler l’excédent d’epoxy séché présent sur les jointures des 2 parties. (20 min)

9- SND-SHRD : A l’aide de différentes épaisseurs de papier à poncer, lisser les jointures des 2 parties de telle manière qu’elle devienne imperceptible au toucher. Une technique consiste à insérer de la colle forte dans les interstices puis rapidement de poncer par-dessus. Les poussières de plastique poncées et mélangées à la colle vont ainsi combler les espaces indésirables. (2h)

10- SND-SHRD : Continuer le ponçage sur toutes les surfaces du shroud en perspective d’une future peinture. (1h)

11- PREP-SPR : Saisir les entretoises hexagonales puis les marquer sur toute leur longueur à l’aide d’une lime biseautée. (30 min)

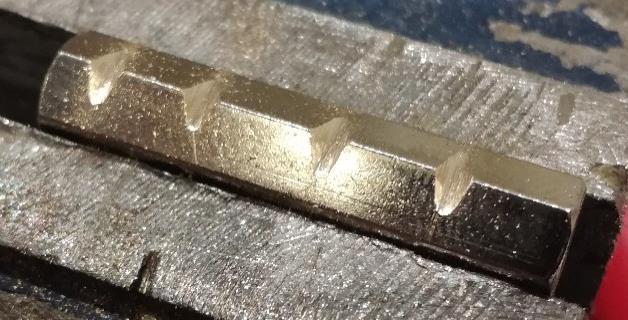
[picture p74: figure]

12- PREP-SHRD : Masquer à l’aide de ruban de masquage les supports de fixation de la turbine. Cette étape permettra d’éviter d’étaler de l’epoxy sur leur surface durant l’étape qui vient. (10 min)

13- PREP-EPXY : Préparer un mélange résine epoxy + durcisseur en tube (attention sèche plus rapidement)

14- ASS-SPR : Visser partiellement les entretoises sur un morceau de tige filetée M3 puis les enduire d’epoxy ainsi que leur logement et les y insérer. Dévisser la tige M3. Cette tige permet d’éviter de s’enduire les mains d’epoxy mais aussi d’insérer plus facilement les entretoises dans leur logement. (15 min)

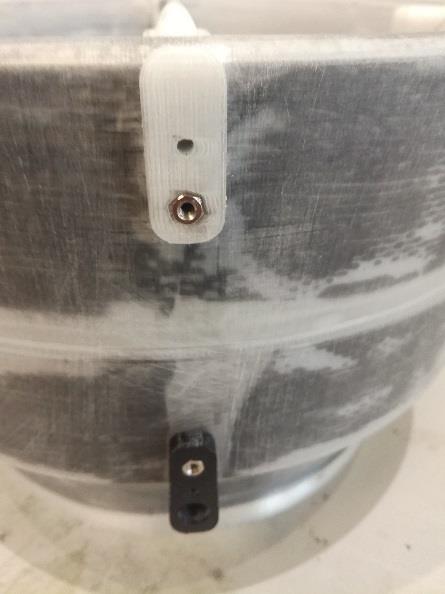
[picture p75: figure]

15- ASS-SPR : Retirer immédiatement le ruban de masquage avant le séchage de l’epoxy. (1 min)

16- DRY-EPXY : Laisser sécher plusieurs heures. (at least 3 hours)

## IX- Finalisation de l’assemblage de la turbine Athena : ASS-TRB

Approx time : 185 min
Matériel nécessaire :
- 2 tiges filetées M3
- 4 connecteurs 3mm mâles
- Gaine thermo rétractable
- Un fer à souder avec étain
- Une scie à métaux
- Une lime
- 8 écrous M3 simples sans Nylstop
- De la colle forte type superglue

1- PREP-M3 : Découper les tiges filetées M3 en huit morceaux : 4 morceaux de longueur 64mm et 4 morceaux de longueur 85mm. Ceux-ci serviront à maintenir les ensembles bras-rotors dans le shroud. (1h)

2- PREP-M3 : Coller avec la superglue un écrou M3 a une seule extrémité de chaque morceau de tige filetée. (20 min)


3- ASS-SHRD-ARM : Positionner les ensemble bras-rotors dans le shroud et faire passer les câbles des ESC dans les trous prévus à cet effet. (30 min)

4- SLD-CON : Souder les connecteurs 3mm mâles sur les fils des ESC qui vont en direction de la batterie. (45 min)

5- ASS-SHRD-ARM : Fixer les ensemble bras-rotors au shroud grâce aux tiges préalablement découpées en respectant la règle suivante : Les tiges de longueur 64mm sont destinées aux bras les plus fins et celles de 85mm de long aux bras les plus épais. A cette étape-ci les rotors devraient toujours être bien coaxiaux et les pales ne doivent pas toucher la surface interne du shroud. (30 min)


La turbine Athena est désormais totalement assemblée. Place maintenant au test de bon fonctionnement

## X- Test de fonctionnement : TEST-TRB

Approx time : 45 min
Matériel nécessaire :
- Une alimentation de tension pour chaque moteur et pilotable à distance.
- Un système de génération de signaux PWM contrôlable à distance
- Un banc de test qui permet la fixation de la turbine
- Un capteur de force
- Un système d’acquisition de données
- Le logiciel Neva Aerospace permettant d’afficher les données collectées

1- ASS-TRB-BNCH : Monter la turbine sur le banc de test (5 min)

2- WRE-TRB : Procéder au branchement des câbles de puissance et des câbles de signaux des ESC. Attention aux polarités ! (5 min)

3- PARAM-ESC : Paramétrer les ESC grâce au logiciel et grâce à la transmission via wifi la tension délivrée par les générateurs de tension. (10 min)

4- VERIF-WRE : Vérifier que tout soit bien branché et faire une inspection visuelle des rotors et du shroud pour prévenir d’un endommagement de la turbine. (5 min)


5- Quitter l’espace de test de la turbine avant la mise sous tension

6- STRT-TEST : Lancer le programme automatisé de test de la turbine. (20 min)

7- Observer les résultats obtenus et vérifier qu’ils correspondent aux modèles déjà obtenus lors de précédents tests avec les mêmes turbines.

## XI- Peinture de la turbine : PNT-TRB

Approx time : 205 min without drying
Matériel nécessaire :
- 1 aérosol d’apprêt spécial plastique gris (400ml)
- 1 aérosol de peinture spécial plastique blanc brillant (400ml)
- 1 aérosol de vernis brillant transparent
- 1 sticker Neva Aerospace
- 1 sticker « this side up »
- 1 sticker « ne pas insérer les mains dans la turbine »
- Une pièce isolée du vent, avec une température constante de 20°C et une humidité n’excédant pas 50%

1- PREP-PNT : Démonter les rotors de la turbine de manière à ne garder que le shroud. (15 min)

2- PREP-PNT : Vérifier l’état de surface du plastique composant le shroud. Celui-ci ne doit comporter aucune irrégularité, doit être propre et bien lisse. Cette étape a normalement été effectuée dans la section « ASS-SHRD » étape 10, page 21.

3- PREP-PNT : Masquer les faces d’appui des bras sur les plugs avec du scotch de peinture, et bien vérifier que les filetages soient masqués eux aussi. (15 min)

4- PREP-PNT : Préparer un support plat ou poser la turbine à l’endroit, et dans la pièce dans laquelle vous allez peindre.

5- PNT-SHRD : Suivre les instructions indiquées sur l’aérosol d’apprêt. Secouer pendant 3 min puis vaporiser sur toutes les surfaces du shroud. La première couche doit être fine. Attendre 15 min entre chaque couche. Vaporiser 2 couches uniformément sur toutes les surfaces. (25 min)

6- DRY-PNT : Laisser sécher 30 min

7- PNT-SHRD : Suivre les instructions indiquées sur l’aérosol de peinture. Secouer pendant 3 min puis vaporiser sur toutes les surfaces du shroud. La première couche doit être fine. Attendre 15 min entre chaque couche. Vaporiser 3 couches uniformément sur toutes les surfaces. (45 min)

8- DRY-PNT : Laisser sécher au minimum 24H

9- LAY-STK : Une fois la peinture sèche, coller les stickers à leur place directement à même la peinture. (5 min)

10- PNT-SHRD : Suivre les instructions indiquées sur l’aérosol de vernis. Secouer pendant 3 min puis vaporiser sur toutes les surfaces du shroud. Vaporiser en 1 couche en faisant attention de ne pas trop insister au même endroit. (10 min)

11- DRY-PNT : Laisser sécher 24H

12- ASS-TRB : Remonter les bras dans le shroud (15 min)

13- TEST-TRB : Procéder à nouveau à un test sur banc. (45 min)

Exemple de turbines Athena montées sur le prototype Wohler B Mark III


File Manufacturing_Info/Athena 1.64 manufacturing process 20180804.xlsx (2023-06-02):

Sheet: Material required PROD-SHRD
PROD-SHRD
Shroud manufacturing
 | Material required:
- | Superior part of the shroud in CPE
- | Bottom Inlet of the shroud in CPE
- | Bottom Outlet of the shroud in CPE
- | CPE gasket
- | 4 plugs set in black CPE
- | Carbon fiber rolls of 10 and 2,5cm width
- | Epoxy mix with 5:1 ratio (resin+hardener)
- | Epoxy packaged in tube
- | 2 or 3 brushes
- | wooden sticks "ice cream" type
- | A stanley knife (cutter)
- | Sanding paper with grit 60, 120, 240, 350, 400
- | 8 spacer bars M3 of 25mm lenght
- | 1 bevelled file
- | 1 rond file
- | 1 drilling machine or dremel with a round sanding nozzle of 1cm diameter
- | M3 threaded rod
- | Superglue
- | Multiple ties
- | A weight of 8-10kg

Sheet: PROD-SHRD
Process | Time
Production of SHRDSUP | 25 min
PREP-SHRDSUP : Prepare superior part of the shroud after it is finished to be 3D printed. Remove imperfections with a cutter | 5 min
PREP-CRB : Cut carbon fiber strips in the rolls in order to fill internal surfaces of the superior part | 5 min
PREP-EPXY : Prepare an epoxy mix with 5:1 ratio
EPXY-SHRDSUP : Spread epoxy inside the superior part using a brush, place carbon fiber strips and then pass a second layer of epoxy on it | 15 min
DRY-SHRDSUP : Leave to dry for one night. | at least 12h
Production of SHRDINF | 170 min
PREP-PLG : Prepare black CPE plugs when finished to be 3D printed. Use a cutter to remove imperfections. Make sure each pair of plug fits | 1h30 min
PREP-SHRDINF :Prepare the two bottom parts that make up the shroud inferior the same way as previously using a cutter | 10 min
DRML-PLG : Using a dremel or a drill with the rond sanding nozzle, enlarge the wholes where the plugs will be inserted. Make sure they can be inserted easily | 20 min
ASS-PLG-SHRDINF :Insert the plugs in order to assemble the two parts composing the shroud inferior | 10 min
ADJ-RTR-SHRDINF : Using a rotor mounted on its arm, position it on its housing using M3 threaded rods and tighten it. Before, you will need to insert a spacer of 0,5mm thick between the plugs and the tip of the finnest arms This step is to verify and adjust the game between the tip of the blades and inlet surface of shroud inferior. | 30 min
ADJ-SHRDINF-SHRDSUP : Temporarly mount the CPE gasket and shroud superior on shroud inferior always in order to verify and adjust the game. | 10 min
ADJ-SHRDINF-SHRDSUP : Once it is done, remove the CPE gasket and the shroud superior but let the rotor mounted. Then go to next step.
Assembly of SHRD | 316 min
PREP-CRB : Cut carbon fiber strips in order to fill internal surfaces of the shroud inferior | 10 min
PREP-TIE : Prepare 2 collars made with ties with a diameter a little bit bigger than the shroud diameter | 10 min
PREP-EPXY : Prepare an epoxy mix with 5:1 ratio
EPXY-SHRDINF : Spread expoxy inside the shroud inferior using a brush and place carbon fiber strips in order to cover all the inside. Then spread epoxy again on it. Once it is done, immediately mount and center the CPE gasket. Then spread epoxy on centering edges of both shroud parts and join the two parts beeing careful to align on the same vertical axis the wholes where ESC wires are supposed to pass through. To get the best alignment, insert M3 threaded rod in each fixation wholes of the turbine and align it using a square. | 30 min
TIE-SHRD : Place ties collars around the shroud and insert a maximum of wooden sticks between ties collars and external surface of the shroud | 10 min
WGT-SHRD : Add a weight on the top of the shroud to apply pressure during the time required for epoxy to dry.
DRY-EPXY : Leave to dry for a night. | at least 12 h
PREP-SHRD : Once dry, remove the weight, collar ties and wooden sticks. Then with a sharp blade scrape off the surplus of epoxy present on joints of the shroud. | 20 min
SND-SHRD : Using differents thicknesses of sanding paper, smooth the joints to ensure that it becomes imperceptible to the touch. A good technic consists to insert superglue in imperfections then sand quickly on it. Plastic dust created by sanding will mix with the superglue and fill interstices. | 2h
SND-SHRD : Continue sanding on all surfaces of the shroud in perspective of a future paint job. | 1h
PREP-SPR : Hold hexa spacer bars then make notches on it using a bevelled file. | 30 min
PREP-SHRD : Mask using masking tape fixation supports of the turbine. This step will prevent to spread epoxy on their surface during following step. | 10 min
PREP-EPXY :prepare a mix of epoxy using epoxy packaged in tubes this time
ASS-SPR : Partially screw the hexa spacer bars on a M3 threaded rod then spread epoxy on it as well as on their housing and insert it. Then unscrew the M3 rod. | 15 min
ASS-SPR : Immediately remove masking tape | 1 min
DRY-EPXY :Leave to dry for at least 3 hours | at least 3h

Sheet: Material required ASS-TRB
ASS-TRB
Turbine assembly
 | Material required:
- | 2 M3 threaded rods
- | 4 male 3mm connectors
- | Heat shrink tubing
- | A soldering iron
- | A hacksaw
- | 8 simple M3 nuts without Nylstop
- | Superglue

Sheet: ASS-TRB
Process | Time
Assembly of TRB | 185 min
PREP-M3 : Cut M3 threaded rods in 8 pieces : 4 pieces 64mm lenght and 4 pieces 85mm lenght. | 1h
PREP-M3 : Glue a nut on a single tip of each M3 rod beforehand cut. | 20 min
ASS-SHRD-ARM : Position the rotors in the shroud and pass the ESCs cables through the wholes of the plugs. | 30 min
SLD-CON : Sold 3mm connectors on ESCs red and black wires going to the battery | 45 min
ASS-SHRD-ARM : Tighten the arms to the shroud using M3 rods beforehand cut respecting following rule : 64mm rods are provided for thinnest arms while 85mm rods are for thicker arms. At the end of this step, both rotors should be coaxials and blades shouldn't touch the shroud. If this is the case so play with clamping until you find a good alignment. | 30 min

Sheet: Technical abbreviations
Technical abbreviations
ADJ = Adjustment
ARM = Arm (part)
ASS = Assembly
BLD = Blade (part)
BNCH = Bench
CON = Connector
CRB = Carbon fiber
DRL = Drill
DRML = Dremel
DRY = Dry
EPXY = Epoxy mix (resin + hardener)
ESC = Electronic Speed Controller
HUB = Hub (part)
LAY = Lay
M3 = M3 threaded rod
MTR = Motor
PARAM = Parameter
PLG = Plug (part)
PNT = Paint
PREP = Preparation
PROD = Production
RTR = Rotor (part)
SHRD = Shroud
SHRDINF = Shroud inferior
SHRDSUP = Shroud superior
SLD = Solder
SND = Sand
SPR = Spacer bar
STK = Sticker
STRT = Start
TEST = Test
TIE = Tie (collar)
TRB = Turbine Athena
VERIF = Verification
WGT = Weight
WRE = Wire

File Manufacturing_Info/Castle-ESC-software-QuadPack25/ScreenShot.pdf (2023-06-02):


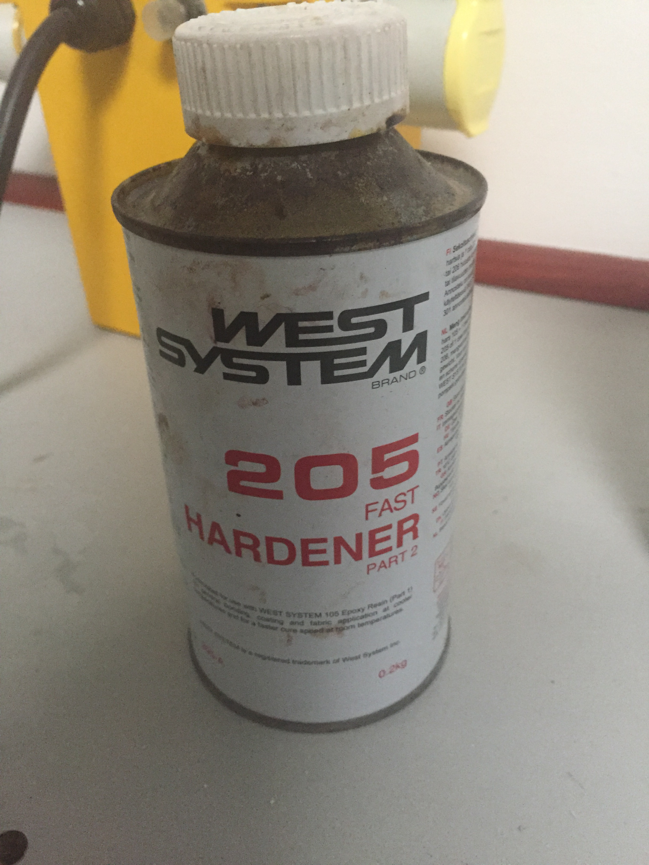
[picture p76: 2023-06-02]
Manufacturing_Info/Epoxy_HardenerWest_System_205_IMG_6318.JPG

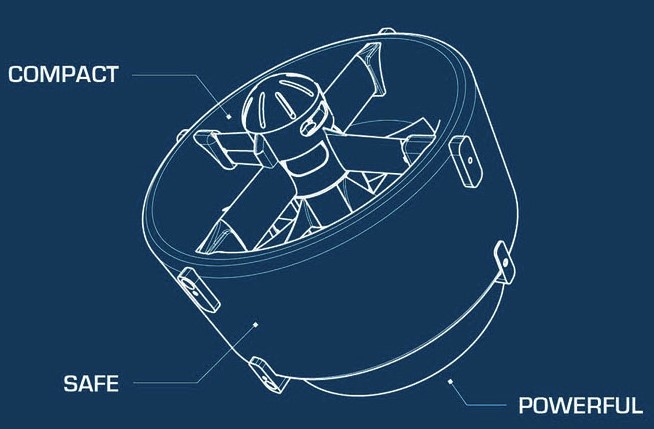
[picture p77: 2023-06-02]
Extra_Docs/Athena-A-2ET_1.6x_BluePrint_night_style.jpg

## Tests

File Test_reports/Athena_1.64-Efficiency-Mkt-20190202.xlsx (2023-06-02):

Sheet: Athena-A2ET-V1.62-6S
 |  |  |  |  |  |  |  | Standard Gravity | 9.80665
Efficiency Thrust vs Power - Athena-A-2ET-V1.64 (6S) |  |  |  |  |  | 6S Data
 |  |  |  |  |  |  | Athena-A-2ET-V1.62 - Thrust - Newton thrust vs Watt Elec
Watt elec. | Newton | N/Kwe | Kgf | Kgf/kWe | Lbf | Lbf/kWe
200 | 11.31 | 56.55 | 1.15 | 5.77 | 2.54 | 12.71 |  | 2.5426011
300 | 15.00 | 50.00 | 1.53 | 5.10 | 3.37 | 11.24
400 | 18.29 | 45.72 | 1.87 | 4.66 | 4.11 | 10.28
500 | 20.92 | 41.84 | 2.13 | 4.27 | 4.70 | 9.41
600 | 24.47 | 40.78 | 2.50 | 4.16 | 5.50 | 9.17
700 | 26.71 | 38.16 | 2.72 | 3.89 | 6.00 | 8.58
800 | 28.68 | 35.85 | 2.92 | 3.66 | 6.45 | 8.06
900 | 31.58 | 35.09 | 3.22 | 3.58 | 7.10 | 7.89
1020 | 33.29 | 32.64 | 3.39 | 3.33 | 7.48 | 7.34
1118 | 36.40 | 32.56 | 3.71 | 3.32 | 8.18 | 7.32
1230 | 39.98 | 32.50 | 4.08 | 3.31 | 8.99 | 7.31
Watt | Kgf/Kw
200 | 5.77
300 | 5.10
400 | 4.66
500 | 4.27
600 | 4.16
700 | 3.89
800 | 3.66
900 | 3.58
1000 | 3.33
1118 | 3.32
1230 | 3.31
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

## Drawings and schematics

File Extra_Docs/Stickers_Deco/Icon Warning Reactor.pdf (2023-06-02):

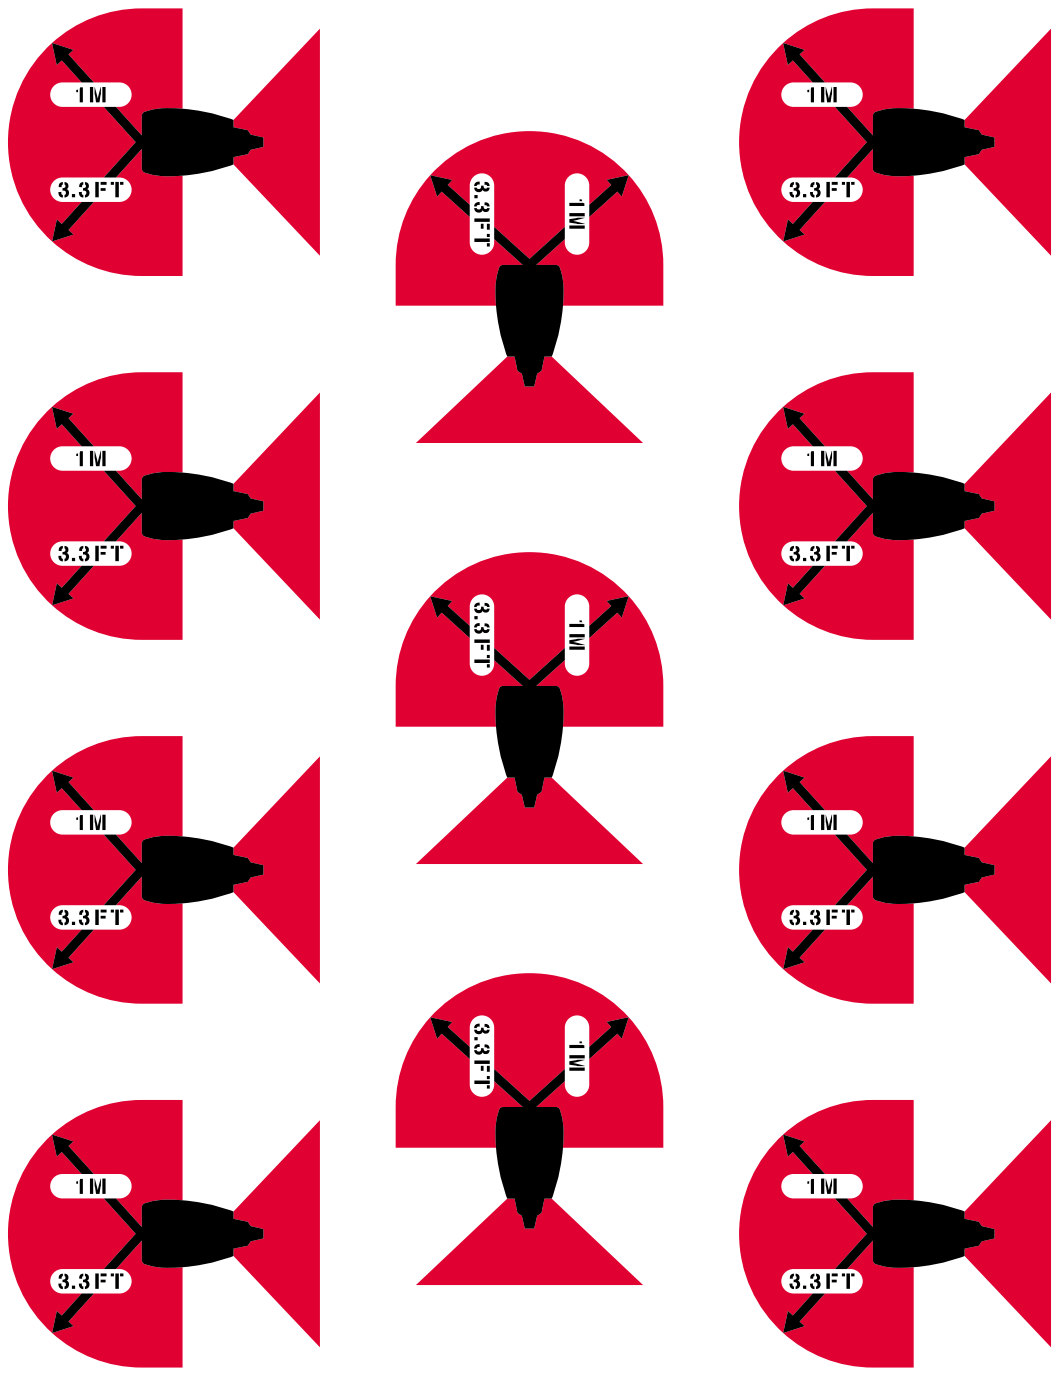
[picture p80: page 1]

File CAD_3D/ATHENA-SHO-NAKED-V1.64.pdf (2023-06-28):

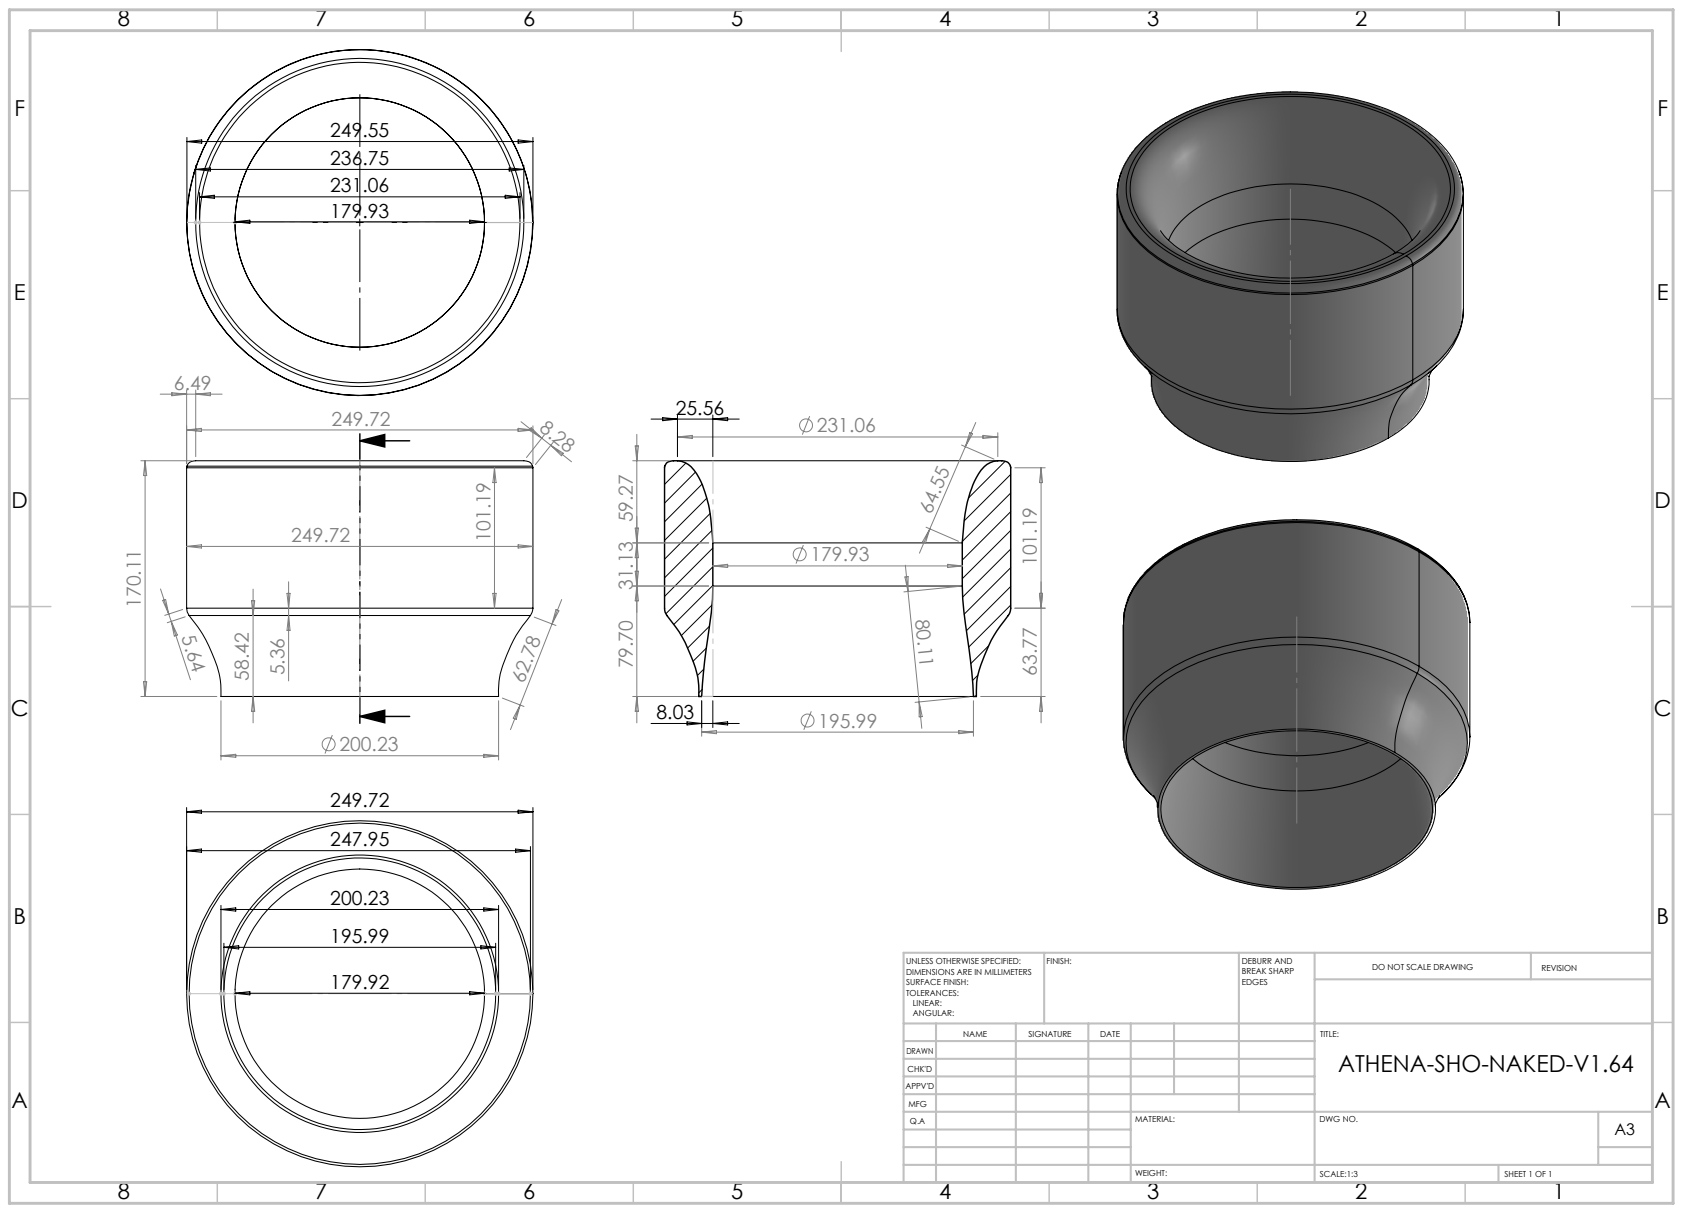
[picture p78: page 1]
FINISH:; DEBURR AND; BREAK SHARP; DO NOT SCALE DRAWING; REVISION; SCALE:1:3; SHEET 1 OF 1

UNLESS OTHERWISE SPECIFIED:
DIMENSIONS ARE IN MILLIMETERS
SURFACE FINISH:
TOLERANCES:
LINEAR:
ANGULAR:

NAME | SIGNATURE | DATE | | | | TITLE: ATHENA-SHO-NAKED-V1.64

DRAWN
CHK'D
APPV'D
MFG
Q.A | | | | MATERIAL: | DWG NO. | A3

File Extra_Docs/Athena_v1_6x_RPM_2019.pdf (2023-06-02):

# Athena V1.6 : RPM vs Power

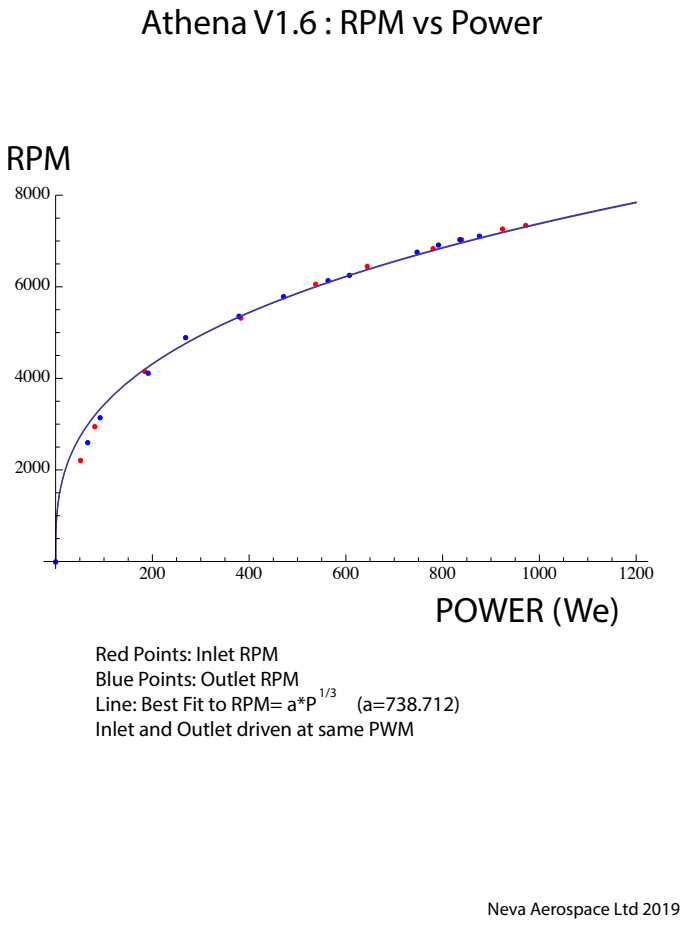
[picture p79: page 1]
RPM; POWER (We); Line: Best Fit to RPM= a*P

Red Points: Inlet RPM
Blue Points: Outlet RPM
Inlet and Outlet driven at same PWM

Neva Aerospace Ltd 2019
